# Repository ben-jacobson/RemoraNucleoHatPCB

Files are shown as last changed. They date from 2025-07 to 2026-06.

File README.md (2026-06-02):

# Remora Nucleo-144 Hat PCB.
Work in progress design for a cost-effective, highly customisable LinuxCNC motion control unit.

Form factor is a hat/shield for ST Nucleo-144 evaluation board running [Remora](https://github.com/scottalford75/Remora). Requires a WIZNet TOE for Ethernet control. A link to a specific recommended version of Remora can be found below but other versions should work. This unit is capable of controlling a variety of machine types including CNC milling machines, routers, lathes, laser and plasma cutters. 

Schematics and board layout are editable with Kicad 9. Gerbers and PDF's of the schematics will become available on release. At this stage the design is pre-release with a lot of validation/testing/design work pending. 

## Proposed Features
- **Low cost**: Board can be fabricated via PCBWay, parts can be ordered from Digikey/Mouser/Element14. Digikey part numbers are written into the BOM for easy ordering. My latest build was sponsored by PCBWay but their estimated cost was just under the $100USD mark not including shipping 
- **Approachable**: Goal is to be well documented, providing step by step build guides.
- **Moderate skill requirement**: SMT soldering skills are required but the pad sizes are forgiving enough for hand soldering. Hot air or reflow oven soldering is possible but not required. 

## Current spec
- Nucleo-144 Hat for 6 axis LinuxCNC motion control using custom port of Remora built for STM32. Board may also support GrblHAL but is not yet tested. 
- Up to 6 axes of isolated, step generation. Default max step gen rate in Remora is 40Khz but the driver circuitry has been tested to generate clean step pulses up to 100Khz. Can be used with any 5V single ended or differential stepper driver. Unused axes can be reconfigured as differential digital outputs. 
- IO: 16x digital inputs, 8x NPN digital outputs. Outputs are sink logic/open collector, protected by a fuse and can sink up to 40mA of current. 
- Most outputs can be configured to drive PWM signals, see the readme in the firmware below for available pins and how to configure this.
- IO: 2x analog inputs (non isolated)
- 1x 0-5v / 0-10v DAC for spindle control. Additional spindle control such as direction or indexing can be achieved with IO.
- 24V DC power input for powering the Nucleo which in turn supplies 5V and 3.3V to sections of the board that are isolated. Galvanic isolation between Nucleo and external devices is achieved by supplying your own isolated 24V supply to the separate input. A jumper can be configured on board to powering the board with only one supply, but will break the isolation.  
- Console logging is available via a UART header (TX only, RX is not used by firmware).

## Future Specs
- PSU's seem to be fine handling 18-28V, need to test this before officially marking this as in spec. 
- There is an experimental single ended ABZ Rotary Encoder Input, it was hobbled together from parts already available on the BOM as an experiment. Predictably it does not perform any high speed task, it would probably even struggle with a slowly moved rotary encoder pot. Will eventually replace with a real design. 

## Build guide
This is intended to be a DIY project, not as a complete product.
A link will soon be provided to a place to order on PCBWay, or you can self source the parts using the DigiKey part numbers.
Please see the jumper settings and connecting to USB section as they are contain important information needed to get started.

**Jumper settings:**
Before powering on your Nucleo hat, ensure that the following two jumpers are set: 
JP1: Please remove this jumper entirely
JP3: Place to the far right position, indicating VIN as per the picture in JP3Setting.png

**Connecting to USB:**
Take care when connecting the device to USB. Please make sure that the board is fully powered up before connecting to USB. Failing to do so could result in damage to your computer. This is not an issue with our design, but in the Nucleo itself. For more info see 7.4.2 in the Nucleo 144 datasheet. The device does not need USB to run. USB can be used to flash new firmware or monitor serial output. For serial output, the provided TX pin header is a better choice if you'd like constant serial monitoring during use.

## Todos
- Perform full board testing with a real load and measure current draws, re-design the PSU's for beter efficiency, line/load regulation, ripple rejection, etc. 
- Add PTC resettable fuses to PSU
- Commit release Gerber files to repo and PDF
- Put up some photos of the completed PCB.
- Put up marketplace product on PCBWay
- Research how we might be able to support Servo drives
- Test GRBLHal

## If you'd like to contribute into this project
Reach out - would love some help with any improvement. Would be especially grateful for anyone willing to help with testing, further engineering support, etc.

## Firmware
Firmware can be found in separate repo: https://github.com/ben-jacobson/Remora-STM32F4xx-PIO

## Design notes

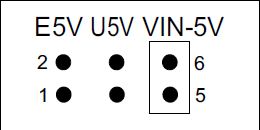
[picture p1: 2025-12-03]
JP3Setting.png

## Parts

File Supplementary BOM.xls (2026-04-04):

Manufacturer | Manufacturer Part Number | Schematic reference | Description | Digikey Part Number | QTY | URL | Per unit cost (AUD at time) | BOM Cost (AUD at time) | Notes | Total Cost (AUD at time) | $42.86
STMicroelectronics | NUCLEO-F446ZE | N/A | STM32F446 Nucleo-144 STM32F4 ARM® Cortex®-M4 MCU 32-Bit Embedded Evaluation Board | 497-16281-ND | 1 | https://www.digikey.com.au/en/products/detail/stmicroelectronics/NUCLEO-F446ZE/5806778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 | $24.56 | $24.56
Wiznet | W5500 Eval Board | N/A | Wiznet Module | N/A | 1 | Ebay/Amazon/AliExpress | - | -
N/A | Nuts and Machine Screws | N/A | Supply own – 5x M2.5 machine screws (3-4mm length). 9x M2.5 Nuts. 2x M3 Nuts | N/A | 1 | N/A | - | -
Würth Elektronik | 971110154 | N/A | 11mm standoff height x M2.5 Standoffs for connecting hat to Nucleo | 732-12923-ND | 4 | https://www.digikey.com.au/en/products/detail/w%C3%BCrth-elektronik/971110154/9488627 | $1.35 | $5.40 | Better value to buy an M2.5 Standoff kit off eBay
Würth Elektronik | 971120154 | N/A | 12mm standoff height x M2.5 Board Standoffs – For mounting Nucleo to DIN Rail mount | 732-12925-ND | 4 | https://www.digikey.com.au/en/products/detail/w%C3%BCrth-elektronik/971120154/9488629 | $1.35 | $5.40
Würth Elektronik | 971200154 | N/A | 20mm Hex Standoff for connecting RPI to hat – M2.5 Brass 0.787" (20.00mm) Silver | 732-12949-ND | 4 | https://www.digikey.com.au/en/products/detail/w%C3%BCrth-elektronik/971200154/9488653 | $1.35 | $5.40
Keystone Electronics | 25503 | N/A | 15mm standoff height x M3 Board Standoffs – 2 for mounting Wiznet Module | 36-25503-ND | 2 | https://www.digikey.com.au/en/products/detail/keystone-electronics/25503/1532182 | $1.05 | $2.10
 | Green = Validated
 | Orange = Altered or yet to be validated
 | Red = Problem, re source

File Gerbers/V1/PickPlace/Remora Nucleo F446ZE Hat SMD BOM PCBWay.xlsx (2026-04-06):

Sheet: Remora Nucleo F446ZE Hat SMD BO
Item # | *Designator | *Qty | Manufacturer | *Mfg Part # | Description / Value | *Package/Footprint | Type | Your Instructions / Notes | US Import Tariff | Note | Part Status | RoHS Status | REACH Status | Moisture Sensitivity Level (MSL) | ECCN | HTSUS | Country of Origin | Environmental Information | Original Part numbers | Unit of Measure | Image | Product Notes
1 | C5,C6 | 2 | Samsung Electro-Mechanics | CL31B105KBHNNNE | CAP CER 1UF 50V X7R 1206 | Capacitor_SMD:C_1206_3216Metric_Pad1.33x1.80mm_HandSolder | SMD | Digikey Part Number: 1276-1068-1-ND |  | - |  | Active | ROHS3 Compliant | REACH Unaffected | 1 (Unlimited) | EAR99 | 8532.24.0020 | Philippines | https://www.samsungsem.com/files/fileDown.do?key=ed1dfdfa-645e-4252-b707-17f9b1502dd1|https://www.samsungsem.com/global/support/certificate/product-stewardship.do | 1276-1068-1-ND | EACH | https://mm.digikey.com/Volume0/opasdata/d220001/medias/images/2537/Ceramic-Capacitor-CL-Series.jpg
2 | C9,C10,C11,C12,C13,C14,C15,C16,C17,C18,C19,C20,C21,C22,C23,C24,C25,C26,C27,C28,C29,C30,C31,C32,C33,C34,C35,C36,C37,C38 | 30 | KEMET | C1206C104K5RACTU | CAP CER 0.1UF 50V X7R 1206 | Capacitor_SMD:C_1206_3216Metric_Pad1.33x1.80mm_HandSolder | SMD | Digikey Part Number: 399-C1206C104K5RACTUCT-ND |  | - |  | Active | ROHS3 Compliant | REACH Unaffected | 1 (Unlimited) | EAR99 | 8532.24.0020 | Mexico |  | 399-C1206C104K5RACTUCT-ND | EACH | https://mm.digikey.com/Volume0/opasdata/d220001/medias/images/721/1206-%283216%29.jpg
3 | D1,D2,D5,D6 | 4 | Harvatek Corporation | B1501USD-20D000313U1930 | 3.2(L) X 1.6(W) X 1.1(H)MM | Diode_SMD:D_1206_3216Metric_Pad1.42x1.75mm_HandSolder | SMD | Digikey Part Number: 3147-B1501USD-20D000313U1930CT-ND |  | - |  | Active | ROHS3 Compliant |  | 2A (4 Weeks) | EAR99 | 8541.41.0000 | Taiwan |  | 3147-B1501USD-20D000313U1930CT-ND | EACH | https://mm.digikey.com/Volume0/opasdata/d220001/derivates/6/003/224/421/MFG_B1501_web%28640x640%29.jpg
4 | D3,D4 | 2 | Diodes Incorporated | B330AF-13 | DIODE SCHOTTKY 30V 3A SMAF | Diode_SMD:D_SMA | SMD | Digikey Part Number: B330AF-13DICT-ND |  | - |  | Active | ROHS3 Compliant | REACH Unaffected | 1 (Unlimited) | EAR99 | 8541.10.0080 | Taiwan | https://mm.digikey.com/Volume0/opasdata/d220001/medias/docus/6731/Diode%20RoHS3%20REACH%20247%20Jan%202025%20Statement.pdf | B330AF-13DICT-ND | EACH | https://mm.digikey.com/Volume0/opasdata/d220001/medias/images/6210/31%7ESMAFLAT%7E%7E2.jpg
5 | D7,D8 | 2 | onsemi | SZMMBZ5232BLT1G | DIODE ZENER 5.6V 225MW SOT23-3 | Package_TO_SOT_SMD:SOT-23 | SMD | Digikey Part Number: SZMMBZ5232BLT1GOSCT-ND |  | - |  | Active | ROHS3 Compliant | REACH Unaffected | 1 (Unlimited) | EAR99 | 8541.10.0050 | China | https://www.onsemi.com/site/pdf/RoHS-statement.pdf|https://www.onsemi.com/site/pdf/REACH-compliance-statement.pdf|https://www.onsemi.com/PowerSolutions/MaterialComposition.do?export=pdf&opnId=SZMMBZ5232BLT1G | SZMMBZ5232BLT1GOSCT-ND | EACH | https://mm.digikey.com/Volume0/opasdata/d220001/medias/images/5883/488%7E318-08%7EET%2CL%2CLT%2CSF%2CSN%7E3.jpg
6 | F1,F2,F3,F4,F5,F6,F7,F8,F9,F10,F11 | 11 | Murata Electronics | PRG18BB330MB1RB | PTC RESET FUSE 24V 36MA 0603 | Fuse:Fuse_0603_1608Metric_Pad1.05x0.95mm_HandSolder | SMD | Digikey Part Number: 490-2471-1-ND |  | - |  | Active | ROHS3 Compliant | REACH Unaffected | 1 (Unlimited) | EAR99 | 8533.40.8070 | China |  | 490-2471-1-ND | EACH | https://mm.digikey.com/Volume0/opasdata/d220001/medias/images/2439/490-PTC%20RESET%200603%20SERIES.jpg
7 | L1,L2 | 2 | Bourns Inc. | SDE0805A-680K | FIXED IND 68UH 1.45A 280 MOHM | Inductor_SMD:L_APV_ANR8040 | SMD | Digikey Part Number: SDE0805A-680KCT-ND |  | - |  | Active | ROHS3 Compliant | REACH Unaffected | 1 (Unlimited) | EAR99 | 8504.50.4000 | China | https://mm.digikey.com/Volume0/opasdata/d220001/medias/docus/6657/Bourns%20REACH%20247%20Jan%202025%20Statement.pdf|https://www.bourns.com/docs/rohs-cofc/cofc_sde.pdf?sfvrsn=510e6dd9_2 | SDE0805A-680KCT-ND | EACH | https://mm.digikey.com/Volume0/opasdata/d220001/medias/images/2605/MFG_SDE0805A%20Series.jpg
8 | Q1 | 1 | onsemi | BC847CLT1G | TRANS NPN 45V 0.1A SOT23-3 | Package_TO_SOT_SMD:SOT-23 | SMD | Digikey Part Number: BC847CLT1GOSCT-ND |  | - |  | Active | ROHS3 Compliant | REACH Unaffected | 1 (Unlimited) | EAR99 | 8541.21.0075 | China | https://www.onsemi.com/site/pdf/RoHS-statement.pdf|https://www.onsemi.com/PowerSolutions/MaterialComposition.do?export=pdf&opnId=BC847CLT1G | BC847CLT1GOSCT-ND | EACH | https://mm.digikey.com/Volume0/opasdata/d220001/medias/images/5883/488%7E318-08%7EET%2CL%2CLT%2CSF%2CSN%7E3.jpg
9 | R1,R21,R22,R23,R24,R25,R26,R27,R28,R61,R62,R63,R64,R65,R66,R67,R68,R77,R78,R79,R80,R81,R82,R83,R84,R89,R90,R95,R96,R97,R100 | 31 | YAGEO | RC1206FR-074K7L | RES 4.7K OHM 1% 1/4W 1206 | Resistor_SMD:R_1206_3216Metric_Pad1.30x1.75mm_HandSolder | SMD | Digikey Part Number: 311-4.70KFRCT-ND |  | - |  | Active | ROHS3 Compliant | REACH Unaffected | 1 (Unlimited) | EAR99 | 8533.21.0030 | Taiwan | https://www.yageogroup.com/content/Resource%20Library/Product%20Environmental%20Compliance/RoHS_Compliance_YAGEO.pdf | 311-4.70KFRCT-ND | EACH | https://mm.digikey.com/Volume0/opasdata/d220001/medias/images/4322/cut-tape-render.jpg
10 | R2,R3,R10,R11,R12,R13,R14,R15,R16,R17,R18,R19,R20,R29,R30,R31,R32,R33,R34,R35,R36,R37,R38,R39,R40,R41,R42,R43,R44,R45,R46,R47,R48,R49,R50,R51,R52,R53,R54,R55,R56,R57,R58,R59,R60,R69,R70,R71,R72,R73,R74,R75,R76,R94 | 54 | YAGEO | RC1206FR-07180RL | RES 180 OHM 1% 1/4W 1206 | Resistor_SMD:R_1206_3216Metric_Pad1.30x1.75mm_HandSolder | SMD | Digikey Part Number: 311-180FRCT-ND |  | - |  | Active | ROHS3 Compliant | REACH Unaffected | 1 (Unlimited) | EAR99 | 8533.21.0030 | Taiwan | https://www.yageogroup.com/content/Resource%20Library/Product%20Environmental%20Compliance/RoHS_Compliance_YAGEO.pdf | 311-180FRCT-ND | EACH | https://mm.digikey.com/Volume0/opasdata/d220001/medias/images/4842/Yageo-0603.jpg
11 | R85,R86,R87,R88,R91,R92,R93,R99,R101 | 9 | Stackpole Electronics Inc | RMCF1206JT1K20 | RES 1.2K OHM 5% 1/4W 1206 | Resistor_SMD:R_1206_3216Metric_Pad1.30x1.75mm_HandSolder | SMD | Digikey Part Number: RMCF1206JT1K20CT-ND |  | - |  | Active | ROHS3 Compliant | REACH Unaffected | 1 (Unlimited) | EAR99 | 8533.21.0030 | China | https://www.seielect.com/catalog/SEI-RoHS_Compliance_Status.pdf|https://www.seielect.com/catalog/reach.pdf|https://www.seielect.com/catalog/sei-coc%20prop%2065.pdf | RMCF1206JT1K20CT-ND | EACH | https://mm.digikey.com/Volume0/opasdata/d220001/medias/images/4849/738_1206.jpg
12 | R98 | 1 | YAGEO | RC1206FR-0710KL | RES 10K OHM 1% 1/4W 1206 | Resistor_SMD:R_1206_3216Metric_Pad1.30x1.75mm_HandSolder | SMD | Digikey Part Number: 311-10.0KFRCT-ND |  | - |  | Active | ROHS3 Compliant | REACH Unaffected | 1 (Unlimited) | EAR99 | 8533.21.0030 | Taiwan | https://www.yageogroup.com/content/Resource%20Library/Product%20Environmental%20Compliance/RoHS_Compliance_YAGEO.pdf | 311-10.0KFRCT-ND | EACH | https://mm.digikey.com/Volume0/opasdata/d220001/medias/images/4322/cut-tape-render.jpg
13 | SW1 | 1 | Omron Electronics Inc-EMC Div | B3FS-1002P | SWITCH TACTILE SPST-NO 0.05A 24V | Button_Switch_SMD:SW_SPST_Omron_B3FS-100xP | SMD | Digikey Part Number: SW424CT-ND |  | - |  | Active | ROHS3 Compliant | REACH Unaffected | 1 (Unlimited) | EAR99 | 8536.50.9031 | China |  | SW424CT-ND | EACH | https://mm.digikey.com/Volume0/opasdata/d220001/medias/images/999/B3FS-1002PCHN.jpg
14 | U2 | 1 | UMW | XL1509-12 | IC REG BUCK 5.0V 2A 8SOIC | Package_SO:SOIC-8_3.9x4.9mm_P1.27mm | SMD | Digikey Part Number: 4518-XL1509-12CT-ND |  | - |  | Active | ROHS3 Compliant | REACH Unaffected | 1 (Unlimited) | EAR99 | 8542.39.0060 | China |  | 4518-XL1509-12CT-ND | EACH | https://mm.digikey.com/Volume0/opasdata/d220001/derivates/6/003/215/772/MFG_4518_SOP-8_web%28640x640%29.jpg
15 | U3 | 1 | UMW | XL1509-5.0 | IC REG BUCK 5.0V 2A 8SOIC | Package_SO:SOIC-8_3.9x4.9mm_P1.27mm | SMD | Digikey Part Number: 4518-XL1509-5.0CT-ND |  | - |  | Active | ROHS3 Compliant | REACH Unaffected | 1 (Unlimited) | EAR99 | 8542.39.0060 | China |  | 4518-XL1509-5.0CT-ND | EACH | https://mm.digikey.com/Volume0/opasdata/d220001/derivates/6/003/215/772/MFG_4518_SOP-8_web%28640x640%29.jpg
16 | U4,U6,U7,U8,U9,U10,U11,U12,U14,U17 | 10 | Lite-On Inc. | LTV-247 | OPTOISO 3.75KV 4CH TRANS 16-SO | Package_SO:SOP-16_4.4x10.4mm_P1.27mm | SMD | Digikey Part Number: 160-2255-1-ND |  | - |  | Active | ROHS3 Compliant | REACH Unaffected | 1 (Unlimited) | EAR99 | 8541.49.8000 | China |  | 160-2255-1-ND | EACH | https://mm.digikey.com/Volume0/opasdata/d220001/medias/images/2476/16%20SOIC.jpg
17 | U5,U13,U15 | 3 | Texas Instruments | AM26LS31CDR | IC TRANSCEIVER 4/0 16SOIC | Package_SO:SOIC-16_3.9x9.9mm_P1.27mm | SMD | Digikey Part Number: 296-1010-1-ND |  | - |  | Active | ROHS3 Compliant | REACH Unaffected | 1 (Unlimited) | EAR99 | 8542.39.0070 | Mexico |  | 296-1010-1-ND | EACH | https://mm.digikey.com/Volume0/opasdata/d220001/medias/images/3982/296%7E4040047-6%7ED%7E16.JPG
18 | U16 | 1 | Microchip Technology | MCP6042T-E/MSVAO | IC OPAMP GP 2 CIRCUIT 8SOIC | Package_SO:SOIC-8_3.9x4.9mm_P1.27mm | SMD | Digikey Part Number: 150-MCP6042T-E/MSVAOCT-ND |  | - |  | Active | ROHS3 Compliant | REACH Unaffected | 2 (1 Year) | EAR99 | 8542.33.0001 | Thailand | https://ww1.microchip.com/downloads/aemDocuments/documents/corporate-responsibilty/environmental/product-regulatory-information/Semiconductor_EnvCoC.pdf|https://ww1.microchip.com/downloads/aemDocuments/documents/corporate-responsibilty/environmental/product-regulatory-information/Microchip_REACH_Statement.pdf | 150-MCP6042T-E/MSVAOCT-ND | EACH | https://mm.digikey.com/Volume0/opasdata/d220001/derivates/6/003/245/611/MFG_150%7EC04-057%7ESN%2COA%7E8_web%28640x640%29.jpg
19 | U18 | 1 | Diotec Semiconductor | MMTL431A | IC VREF SHUNT ADJ 0.5% SOT23-3 | Package_TO_SOT_SMD:SOT-23 | SMD | Digikey Part Number: 4878-MMTL431ACT-ND |  | - |  | Active | ROHS3 Compliant | REACH Unaffected | Not Applicable | EAR99 | 8542.39.0070 | China | https://diotec.com/request/imds/p200_e.pdf | 4878-MMTL431ACT-ND | EACH | https://mm.digikey.com/Volume0/opasdata/d220001/derivates/6/003/243/004/MFG_4878%7ESOT23-3%7E%7E3_web%28640x640%29.jpg

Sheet: Sheet2
 |  |  | Remora Nucleo F446ZE Hat BOM
Item # | *Designator | *Qty | Manufacturer | *Mfg Part # | Description / Value | *Package/Footprint | Type | Your Instructions / Notes
1 | C5,C6 | 2 | Samsung Electro-Mechanics | CL31B105KBHNNNE | CAP CER 1UF 50V X7R 1206 | Capacitor_SMD:C_1206_3216Metric_Pad1.33x1.80mm_HandSolder | SMD | Digikey Part Number: 1276-1068-1-ND
2 | C9,C10,C11,C12,C13,C14,C15,C16,C17,C18,C19,C20,C21,C22,C23,C24,C25,C26,C27,C28,C29,C30,C31,C32,C33,C34,C35,C36,C37,C38 | 30 | KEMET | C1206C104K5RACTU | CAP CER 0.1UF 50V X7R 1206 | Capacitor_SMD:C_1206_3216Metric_Pad1.33x1.80mm_HandSolder | SMD | Digikey Part Number: 399-C1206C104K5RACTUCT-ND
3 | D1,D2,D5,D6 | 4 | Harvatek Corporation | B1501USD-20D000313U1930 | 3.2(L) X 1.6(W) X 1.1(H)MM | Diode_SMD:D_1206_3216Metric_Pad1.42x1.75mm_HandSolder | SMD | Digikey Part Number: 3147-B1501USD-20D000313U1930CT-ND
4 | D3,D4 | 2 | Diodes Incorporated | B330AF-13 | DIODE SCHOTTKY 30V 3A SMAF | Diode_SMD:D_SMA | SMD | Digikey Part Number: B330AF-13DICT-ND
5 | D7,D8 | 2 | onsemi | SZMMBZ5232BLT1G | DIODE ZENER 5.6V 225MW SOT23-3 | Package_TO_SOT_SMD:SOT-23 | SMD | Digikey Part Number: SZMMBZ5232BLT1GOSCT-ND
6 | F1,F2,F3,F4,F5,F6,F7,F8,F9,F10,F11 | 11 | Murata Electronics | PRG18BB330MB1RB | PTC RESET FUSE 24V 36MA 0603 | Fuse:Fuse_0603_1608Metric_Pad1.05x0.95mm_HandSolder | SMD | Digikey Part Number: 490-2471-1-ND
7 | L1,L2 | 2 | Bourns Inc. | SDE0805A-680K | FIXED IND 68UH 1.45A 280 MOHM | Inductor_SMD:L_APV_ANR8040 | SMD | Digikey Part Number: SDE0805A-680KCT-ND
8 | Q1 | 1 | onsemi | BC847CLT1G | TRANS NPN 45V 0.1A SOT23-3 | Package_TO_SOT_SMD:SOT-23 | SMD | Digikey Part Number: BC847CLT1GOSCT-ND
9 | R1,R21,R22,R23,R24,R25,R26,R27,R28,R61,R62,R63,R64,R65,R66,R67,R68,R77,R78,R79,R80,R81,R82,R83,R84,R89,R90,R95,R96,R97,R100 | 31 | YAGEO | RC1206FR-074K7L | RES 4.7K OHM 1% 1/4W 1206 | Resistor_SMD:R_1206_3216Metric_Pad1.30x1.75mm_HandSolder | SMD | Digikey Part Number: 311-4.70KFRCT-ND
10 | R2,R3,R10,R11,R12,R13,R14,R15,R16,R17,R18,R19,R20,R29,R30,R31,R32,R33,R34,R35,R36,R37,R38,R39,R40,R41,R42,R43,R44,R45,R46,R47,R48,R49,R50,R51,R52,R53,R54,R55,R56,R57,R58,R59,R60,R69,R70,R71,R72,R73,R74,R75,R76,R94 | 54 | YAGEO | RC1206FR-07180RL | RES 180 OHM 1% 1/4W 1206 | Resistor_SMD:R_1206_3216Metric_Pad1.30x1.75mm_HandSolder | SMD | Digikey Part Number: 311-180FRCT-ND
11 | R85,R86,R87,R88,R91,R92,R93,R99,R101 | 9 | Stackpole Electronics Inc | RMCF1206JT1K20 | RES 1.2K OHM 5% 1/4W 1206 | Resistor_SMD:R_1206_3216Metric_Pad1.30x1.75mm_HandSolder | SMD | Digikey Part Number: RMCF1206JT1K20CT-ND
12 | R98 | 1 | YAGEO | RC1206FR-0710KL | RES 10K OHM 1% 1/4W 1206 | Resistor_SMD:R_1206_3216Metric_Pad1.30x1.75mm_HandSolder | SMD | Digikey Part Number: 311-10.0KFRCT-ND
13 | SW1 | 1 | Omron Electronics Inc-EMC Div | B3FS-1002P | SWITCH TACTILE SPST-NO 0.05A 24V | Button_Switch_SMD:SW_SPST_Omron_B3FS-100xP | SMD | Digikey Part Number: SW424CT-ND
14 | U2 | 1 | UMW | XL1509-12 | IC REG BUCK 5.0V 2A 8SOIC | Package_SO:SOIC-8_3.9x4.9mm_P1.27mm | SMD | Digikey Part Number: 4518-XL1509-12CT-ND
15 | U3 | 1 | UMW | XL1509-5.0 | IC REG BUCK 5.0V 2A 8SOIC | Package_SO:SOIC-8_3.9x4.9mm_P1.27mm | SMD | Digikey Part Number: 4518-XL1509-5.0CT-ND
16 | U4,U6,U7,U8,U9,U10,U11,U12,U14,U17 | 10 | Lite-On Inc. | LTV-247 | OPTOISO 3.75KV 4CH TRANS 16-SO | Package_SO:SOP-16_4.4x10.4mm_P1.27mm | SMD | Digikey Part Number: 160-2255-1-ND
17 | U5,U13,U15 | 3 | Texas Instruments | AM26LS31CDR | IC TRANSCEIVER 4/0 16SOIC | Package_SO:SOIC-16_3.9x9.9mm_P1.27mm | SMD | Digikey Part Number: 296-1010-1-ND
18 | U16 | 1 | Microchip Technology | MCP6042T-E/MSVAO | IC OPAMP GP 2 CIRCUIT 8SOIC | Package_SO:SOIC-8_3.9x4.9mm_P1.27mm | SMD | Digikey Part Number: 150-MCP6042T-E/MSVAOCT-ND
19 | U18 | 1 | Diotec Semiconductor | MMTL431A | IC VREF SHUNT ADJ 0.5% SOT23-3 | Package_TO_SOT_SMD:SOT-23 | SMD | Digikey Part Number: 4878-MMTL431ACT-ND
Need a quick and accurante quote? Need an efficient production? Please read SMT Ordering Necessary Files & Info in 1 minute. Thank you very much! (https://www.pcbway.com/smt_ordering_guide.html)
Click for Instructions on How to Create a BOM (https://www.pcbway.com/blog/PCB_Assembly/How_to_Build_a_BOM__Bill_Of_Materials_.html)

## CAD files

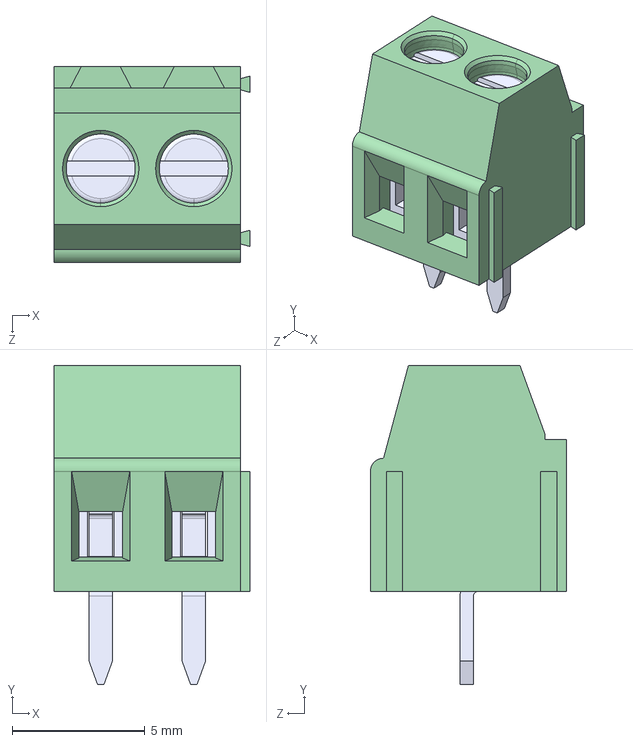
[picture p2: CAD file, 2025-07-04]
Adam Tech Footprints/EBWA_02_A/EBWA-02-A.step
7.37 x 12.0 x 7.39 mm

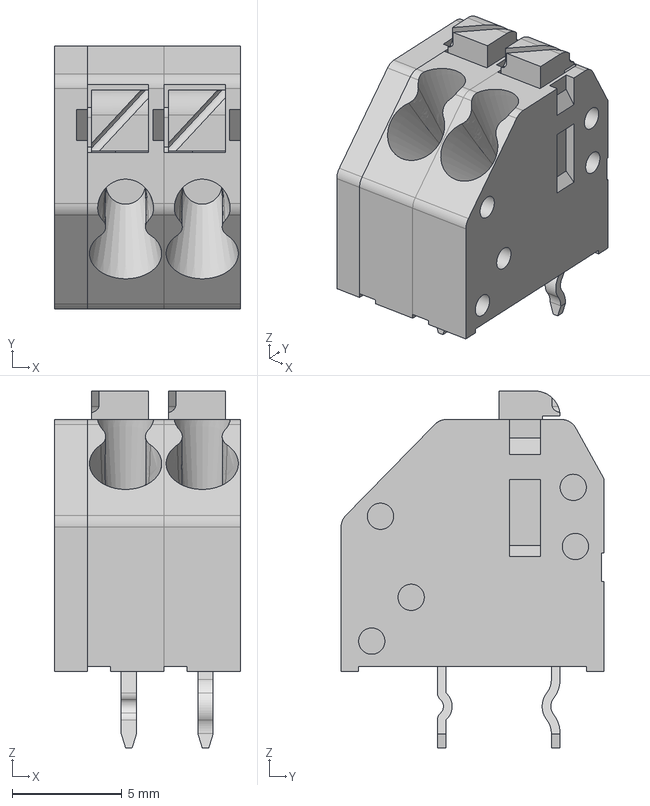
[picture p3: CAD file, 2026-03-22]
TerminalConnectors/691412120002B/Download_STP_691412120002B+(rev1).stp
8.50 x 12.0 x 16.3 mm
6914121200xxB_CAPOT
6914121200xx
6914121200xx_levier x 2
6914121200xxB x 2
6914121200xx_LONG

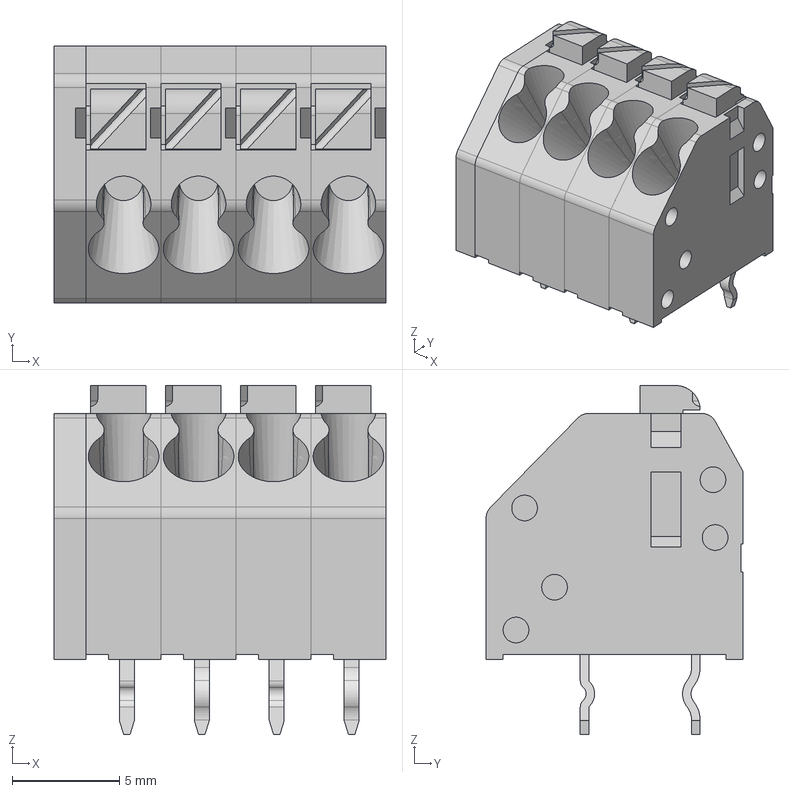
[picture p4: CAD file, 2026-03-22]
TerminalConnectors/691412120004B/691412120004B+(rev1).stp
15.5 x 12.0 x 16.3 mm
6914121200xxB_CAPOT
6914121200xx x 2
6914121200xx_levier x 4
6914121200xxB x 4
6914121200xx_LONG x 2

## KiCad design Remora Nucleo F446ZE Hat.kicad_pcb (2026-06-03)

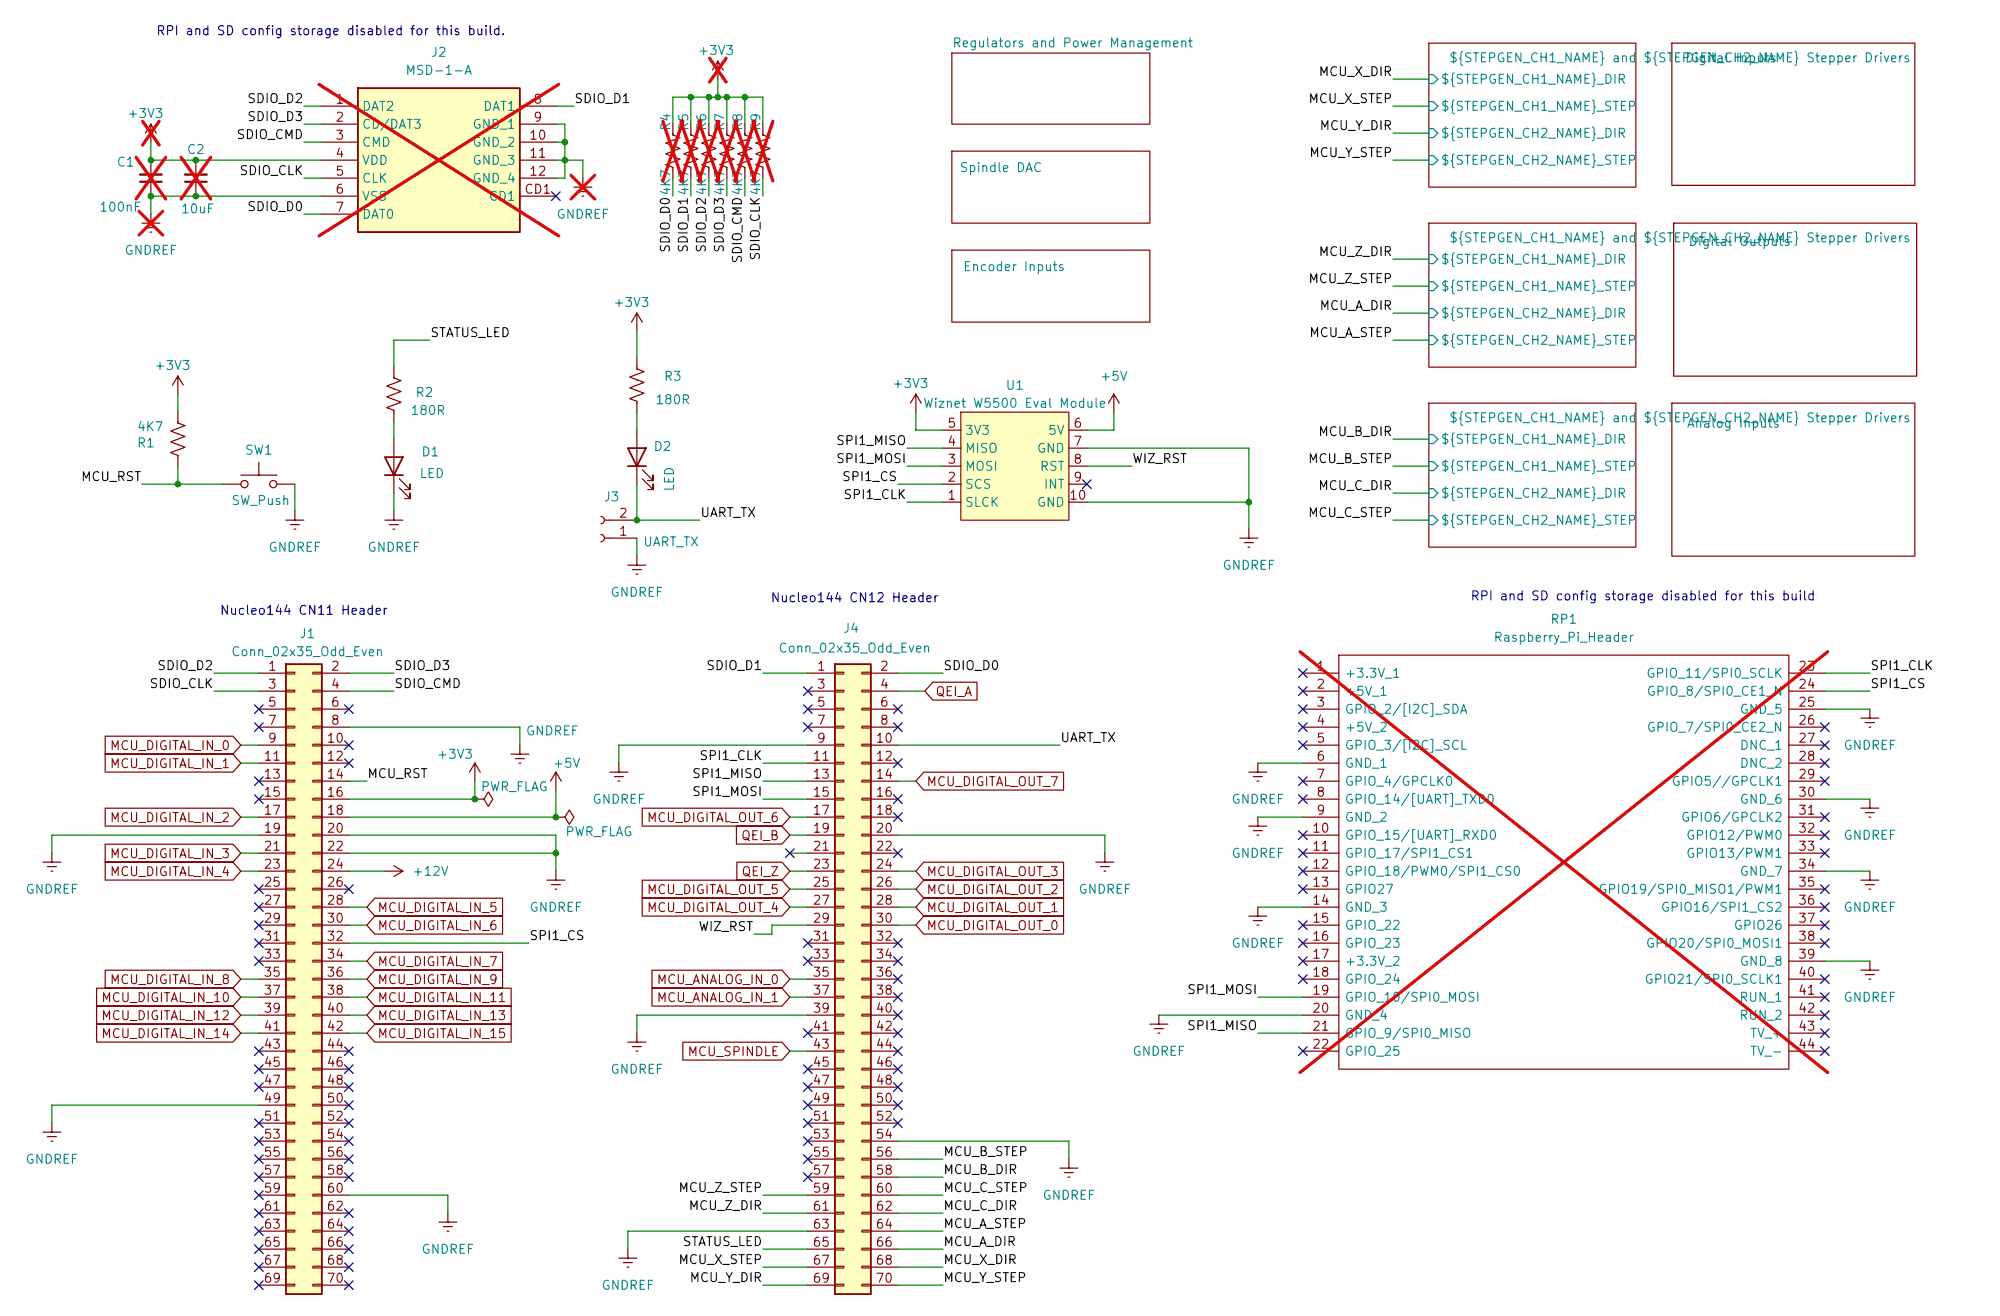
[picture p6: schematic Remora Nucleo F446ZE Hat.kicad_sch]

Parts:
C1: 100nF; C_1206_3216Metric_Pad1.33x1.80mm_HandSolder; Digikey Part Number 399-C1206C104K5RACTUCT-ND; not fitted
C2: 10uF; C_1206_3216Metric_Pad1.33x1.80mm_HandSolder; Digikey Part Number 1276-1804-1-ND; not fitted
D1, D2: LED; D_1206_3216Metric_Pad1.42x1.75mm_HandSolder; Digikey Part Number 3147-B1501USD-20D000313U1930CT-ND
J1, J4: Conn_02x35_Odd_Even; PinHeader_2x35_P2.54mm_Vertical; Digikey Part Number SSW-135-03-T-D-ND
J2: MSD-1-A; MSD1A; Manufacturer_Part_Number MSD-1-A; Mouser Part Number 179-MSD-1-A; not fitted
J3: UART_TX; PinHeader_1x02_P2.54mm_Vertical; Digikey Part Number PH1-02-UA
R1: 4K7; R_1206_3216Metric_Pad1.30x1.75mm_HandSolder; Digikey Part Number 311-4.70KFRCT-ND
R2, R3: 180R; R_1206_3216Metric_Pad1.30x1.75mm_HandSolder; Digikey Part Number 311-180FRCT-ND
R4, R5, R6, R7, R8, R9: 4K7; R_1206_3216Metric_Pad1.30x1.75mm_HandSolder; Digikey Part Number 311-4.70KFRCT-ND; not fitted
RP1: Raspberry_Pi_Header; raspberrypi_2_3; Manufacturer_Part_Number Raspberry Pi 2 or 3; Digikey Part Number SAM1204-20-ND; not fitted
SW1: SW_Push; SW_SPST_Omron_B3FS-100xP; Digikey Part Number SW424CT-ND
U1: Wiznet W5500 Eval Module; W5500EvalModule; Digikey Part Number SAM12520-ND

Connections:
+3V3: C1.2, C2.2, J1.16, J2.4 (VDD), R1.1, R3.1, R4.1, R5.1, R6.1, R7.1, R8.1, R9.1, U1.5 (3V3); also elsewhere on the board
+5V: J1.18, U1.6 (5V)
+12V: J1.24; also elsewhere on the board
/MCU_A_DIR: J4.66; also elsewhere on the board
/MCU_A_STEP: J4.64; also elsewhere on the board
/MCU_B_DIR: J4.58; also elsewhere on the board
/MCU_B_STEP: J4.56; also elsewhere on the board
/MCU_C_DIR: J4.62; also elsewhere on the board
/MCU_C_STEP: J4.60; also elsewhere on the board
/MCU_RST: J1.14, R1.2, SW1.1
/MCU_X_DIR: J4.68; also elsewhere on the board
/MCU_X_STEP: J4.67; also elsewhere on the board
/MCU_Y_DIR: J4.69; also elsewhere on the board
/MCU_Y_STEP: J4.70; also elsewhere on the board
/MCU_Z_DIR: J4.61; also elsewhere on the board
/MCU_Z_STEP: J4.59; also elsewhere on the board
/SDIO_CLK: J1.3, J2.5 (CLK), R9.2
/SDIO_CMD: J1.4, J2.3 (CMD), R8.2
/SDIO_D0: J2.7 (DAT0), J4.2, R4.2
/SDIO_D1: J2.8 (DAT1), J4.1, R5.2
/SDIO_D2: J1.1, J2.1 (DAT2), R6.2
/SDIO_D3: J1.2, J2.2 (CD/DAT3), R7.2
/SPI1_CLK: J4.11, RP1.23 (GPIO_11/SPI0_SCLK), U1.1 (SLCK)
/SPI1_CS: J1.32, RP1.24 (GPIO_8/SPI0_CE1_N), U1.2 (SCS)
/SPI1_MISO: J4.13, RP1.21 (GPIO_9/SPI0_MISO), U1.4 (MISO)
/SPI1_MOSI: J4.15, RP1.19 (GPIO_10/SPI0_MOSI), U1.3 (MOSI)
/STATUS_LED: J4.65, R2.1
/UART_TX: D2.1 (K), J3.2, J4.10
/WIZ_RST: J4.29, U1.8 (RST)
GNDREF: C1.1, C2.1, D1.1 (K), J1.8, J1.19, J1.20, J1.22, J1.49, J1.60, J2.6 (VSS), J2.9 (GND_1), J2.10 (GND_2), J2.11 (GND_3), J2.12 (GND_4), J3.1, J4.9, J4.20, J4.39, J4.54, J4.63, RP1.6 (GND_1), RP1.9 (GND_2), RP1.14 (GND_3), RP1.20 (GND_4), RP1.25 (GND_5), RP1.30 (GND_6), RP1.34 (GND_7), RP1.39 (GND_8), SW1.2, U1.7 (GND), U1.10 (GND); also elsewhere on the board
MCU_ANALOG_IN_0: J4.35; also elsewhere on the board
MCU_ANALOG_IN_1: J4.37; also elsewhere on the board
MCU_DIGITAL_IN_0: J1.9; also elsewhere on the board
MCU_DIGITAL_IN_1: J1.11; also elsewhere on the board
MCU_DIGITAL_IN_2: J1.17; also elsewhere on the board
MCU_DIGITAL_IN_3: J1.21; also elsewhere on the board
MCU_DIGITAL_IN_4: J1.23; also elsewhere on the board
MCU_DIGITAL_IN_5: J1.28; also elsewhere on the board
MCU_DIGITAL_IN_6: J1.30; also elsewhere on the board
MCU_DIGITAL_IN_7: J1.34; also elsewhere on the board
MCU_DIGITAL_IN_8: J1.35; also elsewhere on the board
MCU_DIGITAL_IN_9: J1.36; also elsewhere on the board
MCU_DIGITAL_IN_10: J1.37; also elsewhere on the board
MCU_DIGITAL_IN_11: J1.38; also elsewhere on the board
MCU_DIGITAL_IN_12: J1.39; also elsewhere on the board
MCU_DIGITAL_IN_13: J1.40; also elsewhere on the board
MCU_DIGITAL_IN_14: J1.41; also elsewhere on the board
MCU_DIGITAL_IN_15: J1.42; also elsewhere on the board
MCU_DIGITAL_OUT_0: J4.30; also elsewhere on the board
MCU_DIGITAL_OUT_1: J4.28; also elsewhere on the board
MCU_DIGITAL_OUT_2: J4.26; also elsewhere on the board
MCU_DIGITAL_OUT_3: J4.24; also elsewhere on the board
MCU_DIGITAL_OUT_4: J4.27; also elsewhere on the board
MCU_DIGITAL_OUT_5: J4.25; also elsewhere on the board
MCU_DIGITAL_OUT_6: J4.17; also elsewhere on the board
MCU_DIGITAL_OUT_7: J4.14; also elsewhere on the board
MCU_SPINDLE: J4.43; also elsewhere on the board
unnamed: D1.2 (A), R2.2
unnamed: D2.2 (A), R3.2
QEI_A: J4.4; also elsewhere on the board
QEI_B: J4.19; also elsewhere on the board
QEI_Z: J4.23; also elsewhere on the board

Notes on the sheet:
RPI and SD config storage disabled for this build.
RPI and SD config storage disabled for this build
Nucleo144 CN12 Header
Nucleo144 CN11 Header

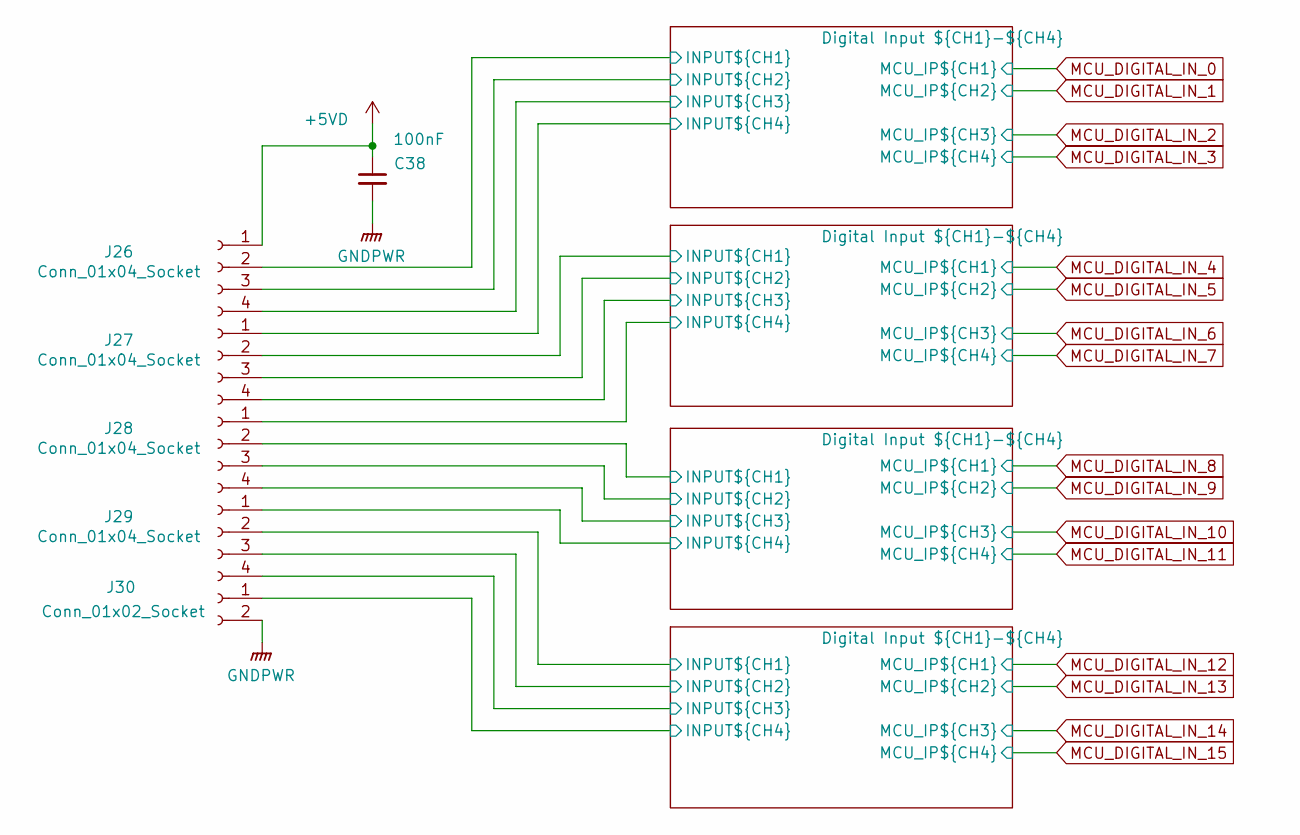
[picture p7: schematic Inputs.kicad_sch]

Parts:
C38: 100nF; C_1206_3216Metric_Pad1.33x1.80mm_HandSolder; Digikey Part Number 399-C1206C104K5RACTUCT-ND
J26, J27, J28, J29: Conn_01x04_Socket; 691412120004B; Digikey Part Number 732-691412120004B-ND
J30: Conn_01x02_Socket; 691412120002B; Digikey Part Number 732-691412120002B-ND

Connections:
+5VD: C38.1, J26.1; also elsewhere on the board
/Digital Inputs/Digital Input 0-3/INPUT0: J26.2; also elsewhere on the board
/Digital Inputs/Digital Input 0-3/INPUT1: J26.3; also elsewhere on the board
/Digital Inputs/Digital Input 0-3/INPUT2: J26.4; also elsewhere on the board
/Digital Inputs/Digital Input 0-3/INPUT3: J27.1; also elsewhere on the board
/Digital Inputs/Digital Input 4-7/INPUT4: J27.2; also elsewhere on the board
/Digital Inputs/Digital Input 4-7/INPUT5: J27.3; also elsewhere on the board
/Digital Inputs/Digital Input 4-7/INPUT6: J27.4; also elsewhere on the board
/Digital Inputs/Digital Input 4-7/INPUT7: J28.1; also elsewhere on the board
/Digital Inputs/Digital Input 8-11/INPUT8: J28.2; also elsewhere on the board
/Digital Inputs/Digital Input 8-11/INPUT9: J28.3; also elsewhere on the board
/Digital Inputs/Digital Input 8-11/INPUT10: J28.4; also elsewhere on the board
/Digital Inputs/Digital Input 8-11/INPUT11: J29.1; also elsewhere on the board
/Digital Inputs/Digital Input 12-15/INPUT12: J29.2; also elsewhere on the board
/Digital Inputs/Digital Input 12-15/INPUT13: J29.3; also elsewhere on the board
/Digital Inputs/Digital Input 12-15/INPUT14: J29.4; also elsewhere on the board
/Digital Inputs/Digital Input 12-15/INPUT15: J30.1; also elsewhere on the board
GNDPWR: C38.2, J30.2; also elsewhere on the board

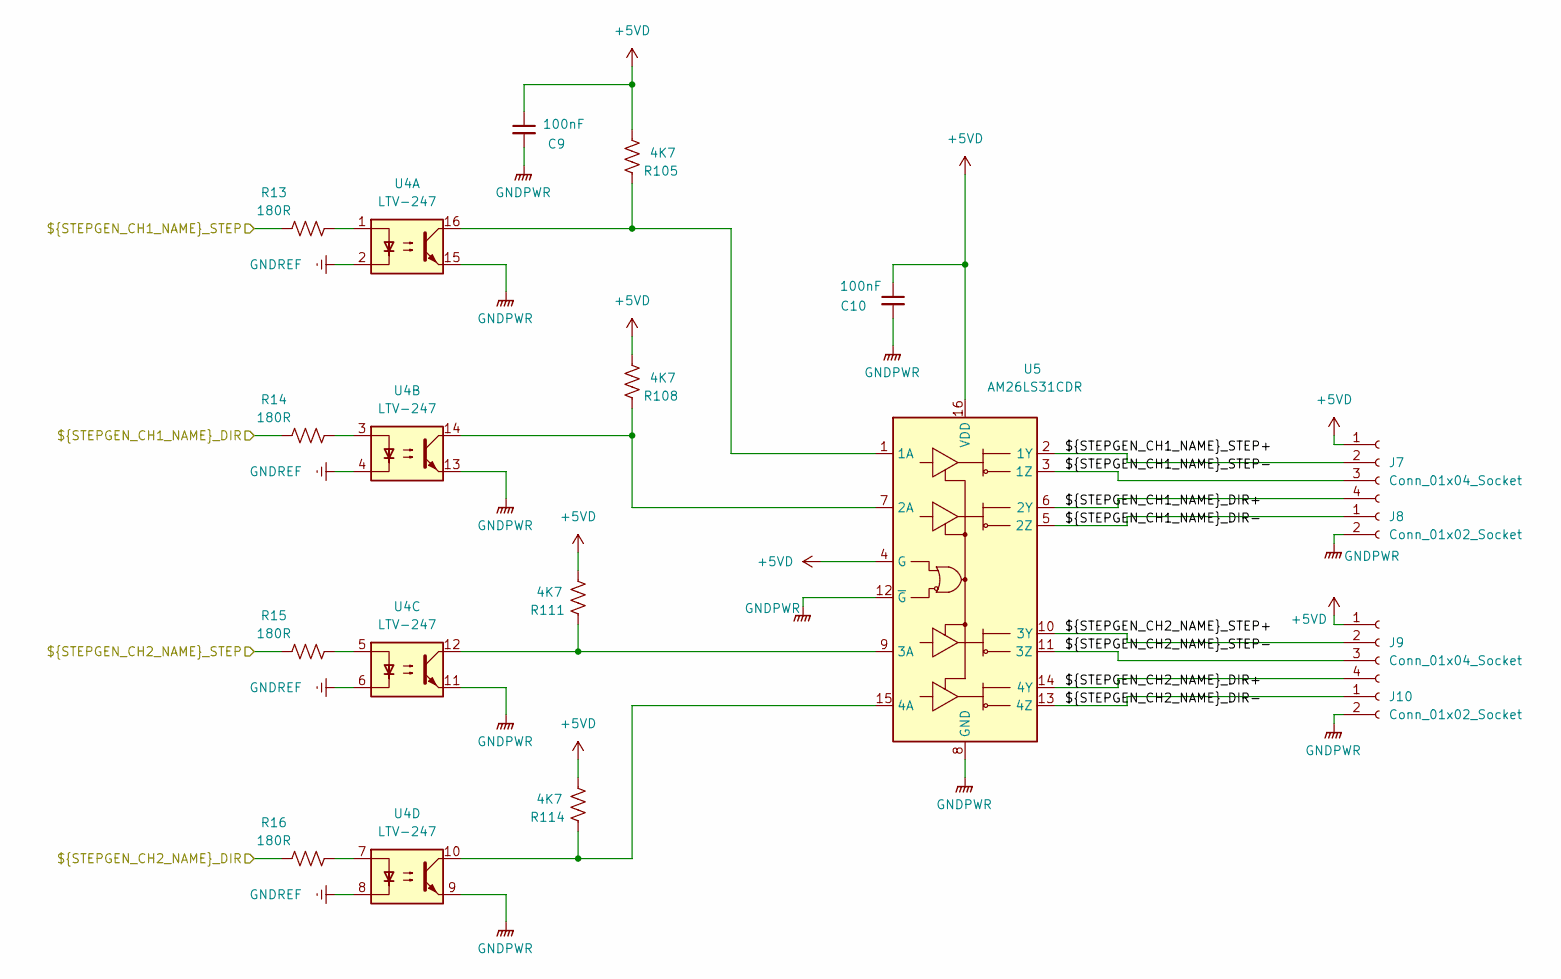
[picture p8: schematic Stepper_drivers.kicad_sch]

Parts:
C9, C10: 100nF; C_1206_3216Metric_Pad1.33x1.80mm_HandSolder; Digikey Part Number 399-C1206C104K5RACTUCT-ND
J7, J9: Conn_01x04_Socket; 691412120004B; Digikey Part Number 732-691412120004B-ND
J8, J10: Conn_01x02_Socket; 691412120002B; Digikey Part Number 732-691412120002B-ND
R13, R14, R15, R16: 180R; R_1206_3216Metric_Pad1.30x1.75mm_HandSolder; Digikey Part Number 311-180FRCT-ND
R105, R108, R111, R114: 4K7; R_1206_3216Metric_Pad1.30x1.75mm_HandSolder; Digikey Part Number 311-4.70KFRCT-ND
U4: LTV-247; SOP-16_4.4x10.4mm_P1.27mm; Digikey Part Number 160-2255-1-ND
U5: AM26LS31CDR; SOIC-16_3.9x9.9mm_P1.27mm; JLCPCB Part #（optional） C3019542

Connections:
+5VD: C9.1, C10.1, J7.1, J9.1, R105.2, R108.2, R111.2, R114.2, U5.4 (G), U5.16 (VDD); also elsewhere on the board
/MCU_X_DIR: R14.1; also elsewhere on the board
/MCU_X_STEP: R13.1; also elsewhere on the board
/MCU_Y_DIR: R16.1; also elsewhere on the board
/MCU_Y_STEP: R15.1; also elsewhere on the board
/X and Y Stepper Drivers/X_DIR+: J7.4, U5.6 (2Y)
/X and Y Stepper Drivers/X_DIR-: J8.1, U5.5 (2Z)
/X and Y Stepper Drivers/X_STEP+: J7.2, U5.2 (1Y)
/X and Y Stepper Drivers/X_STEP-: J7.3, U5.3 (1Z)
/X and Y Stepper Drivers/Y_DIR+: J9.4, U5.14 (4Y)
/X and Y Stepper Drivers/Y_DIR-: J10.1, U5.13 (4Z)
/X and Y Stepper Drivers/Y_STEP+: J9.2, U5.10 (3Y)
/X and Y Stepper Drivers/Y_STEP-: J9.3, U5.11 (3Z)
GNDPWR: C9.2, C10.2, J8.2, J10.2, U4.9, U4.11, U4.13, U4.15, U5.8 (GND), U5.12 (~G); also elsewhere on the board
GNDREF: U4.2, U4.4, U4.6, U4.8; also elsewhere on the board
unnamed: R13.2, U4.1
unnamed: R14.2, U4.3
unnamed: R15.2, U4.5
unnamed: R16.2, U4.7
unnamed: R105.1, U4.16, U5.1 (1A)
unnamed: R108.1, U4.14, U5.7 (2A)
unnamed: R111.1, U4.12, U5.9 (3A)
unnamed: R114.1, U4.10, U5.15 (4A)

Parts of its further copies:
C15, C16, C21, C22: 100nF; C_1206_3216Metric_Pad1.33x1.80mm_HandSolder; Digikey Part Number 399-C1206C104K5RACTUCT-ND
J11, J13, J15, J17: Conn_01x04_Socket; 691412120004B; Digikey Part Number 732-691412120004B-ND
J12, J14, J16, J18: Conn_01x02_Socket; 691412120002B; Digikey Part Number 732-691412120002B-ND
R53, R54, R55, R56, R69, R70, R71, R72: 180R; R_1206_3216Metric_Pad1.30x1.75mm_HandSolder; Digikey Part Number 311-180FRCT-ND
R106, R107, R109, R110, R112, R113, R115, R116: 4K7; R_1206_3216Metric_Pad1.30x1.75mm_HandSolder; Digikey Part Number 311-4.70KFRCT-ND
U12, U14: LTV-247; SOP-16_4.4x10.4mm_P1.27mm; Digikey Part Number 160-2255-1-ND
U13, U15: AM26LS31CDR; SOIC-16_3.9x9.9mm_P1.27mm; JLCPCB Part #（optional） C3019542

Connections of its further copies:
+5VD: C15.1, C16.1, C21.1, C22.1, J11.1, J13.1, J15.1, J17.1, R106.2, R107.2, R109.2, R110.2, R112.2, R113.2, R115.2, R116.2, U13.4 (G), U13.16 (VDD), U15.4 (G), U15.16 (VDD); also elsewhere on the board
/B and C Stepper Drivers/B_DIR+: J15.4, U15.6 (2Y)
/B and C Stepper Drivers/B_DIR-: J16.1, U15.5 (2Z)
/B and C Stepper Drivers/B_STEP+: J15.2, U15.2 (1Y)
/B and C Stepper Drivers/B_STEP-: J15.3, U15.3 (1Z)
/B and C Stepper Drivers/C_DIR+: J17.4, U15.14 (4Y)
/B and C Stepper Drivers/C_DIR-: J18.1, U15.13 (4Z)
/B and C Stepper Drivers/C_STEP+: J17.2, U15.10 (3Y)
/B and C Stepper Drivers/C_STEP-: J17.3, U15.11 (3Z)
/MCU_A_DIR: R56.1; also elsewhere on the board
/MCU_A_STEP: R55.1; also elsewhere on the board
/MCU_B_DIR: R70.1; also elsewhere on the board
/MCU_B_STEP: R69.1; also elsewhere on the board
/MCU_C_DIR: R72.1; also elsewhere on the board
/MCU_C_STEP: R71.1; also elsewhere on the board
/MCU_Z_DIR: R54.1; also elsewhere on the board
/MCU_Z_STEP: R53.1; also elsewhere on the board
/Z and A Stepper Drivers/A_DIR+: J13.4, U13.14 (4Y)
/Z and A Stepper Drivers/A_DIR-: J14.1, U13.13 (4Z)
/Z and A Stepper Drivers/A_STEP+: J13.2, U13.10 (3Y)
/Z and A Stepper Drivers/A_STEP-: J13.3, U13.11 (3Z)
/Z and A Stepper Drivers/Z_DIR+: J11.4, U13.6 (2Y)
/Z and A Stepper Drivers/Z_DIR-: J12.1, U13.5 (2Z)
/Z and A Stepper Drivers/Z_STEP+: J11.2, U13.2 (1Y)
/Z and A Stepper Drivers/Z_STEP-: J11.3, U13.3 (1Z)
GNDPWR: C15.2, C16.2, C21.2, C22.2, J12.2, J14.2, J16.2, J18.2, U12.9, U12.11, U12.13, U12.15, U13.8 (GND), U13.12 (~G), U14.9, U14.11, U14.13, U14.15, U15.8 (GND), U15.12 (~G); also elsewhere on the board
GNDREF: U12.2, U12.4, U12.6, U12.8, U14.2, U14.4, U14.6, U14.8; also elsewhere on the board
unnamed: R53.2, U12.1
unnamed: R54.2, U12.3
unnamed: R55.2, U12.5
unnamed: R56.2, U12.7
unnamed: R69.2, U14.1
unnamed: R70.2, U14.3
unnamed: R71.2, U14.5
unnamed: R72.2, U14.7
unnamed: R106.1, U12.16, U13.1 (1A)
unnamed: R109.1, U12.14, U13.7 (2A)
unnamed: R112.1, U12.12, U13.9 (3A)
unnamed: R115.1, U12.10, U13.15 (4A)
unnamed: R107.1, U14.16, U15.1 (1A)
unnamed: R110.1, U14.14, U15.7 (2A)
unnamed: R113.1, U14.12, U15.9 (3A)
unnamed: R116.1, U14.10, U15.15 (4A)

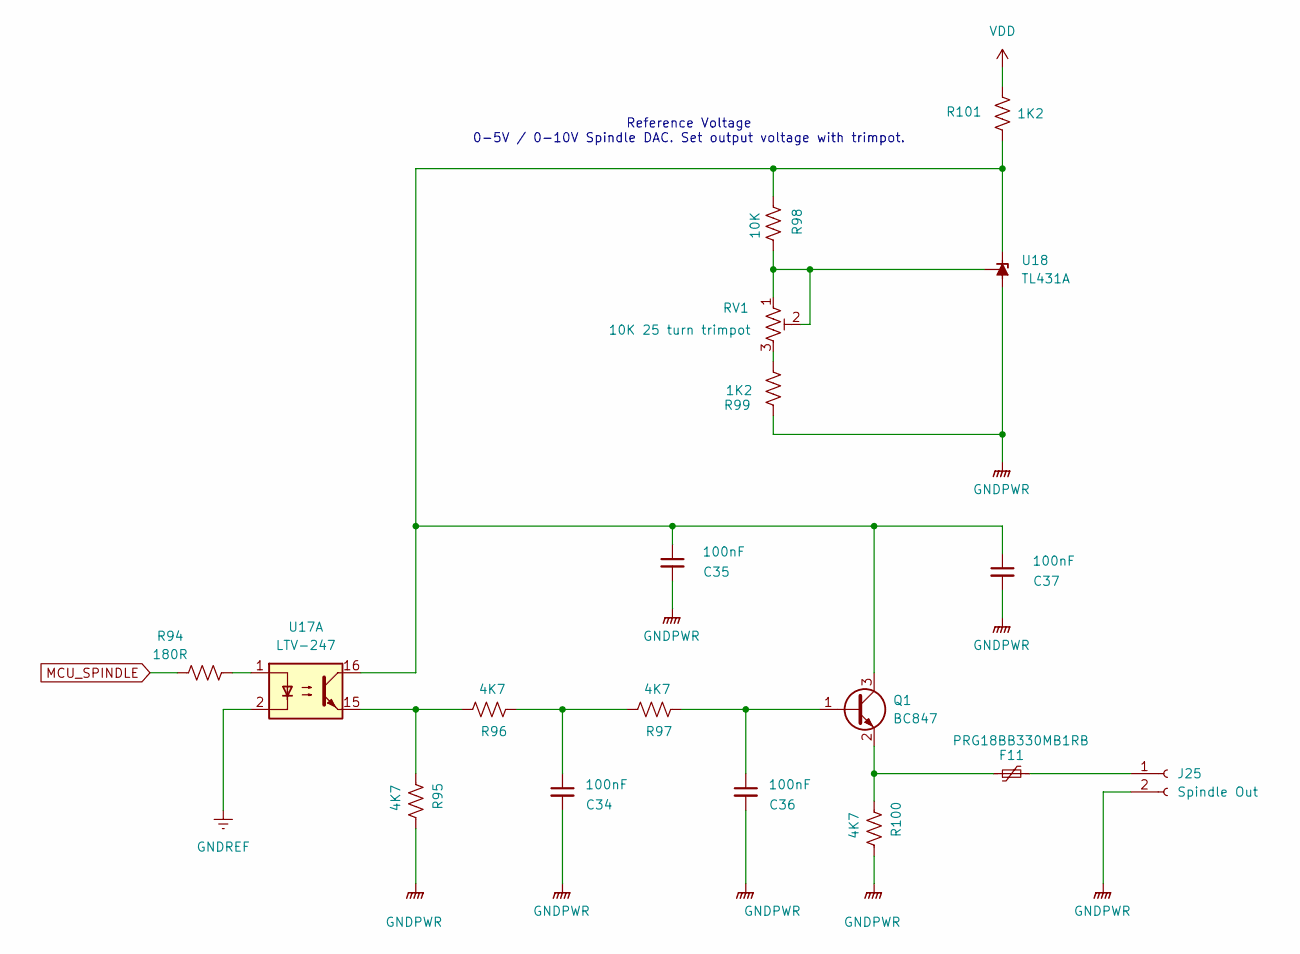
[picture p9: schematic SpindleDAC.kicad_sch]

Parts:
C34, C35, C36, C37: 100nF; C_1206_3216Metric_Pad1.33x1.80mm_HandSolder; Digikey Part Number 399-C1206C104K5RACTUCT-ND
F11: PRG18BB330MB1RB; Fuse_0603_1608Metric_Pad1.05x0.95mm_HandSolder; Digikey Part Number 490-2471-1-ND
J25: Spindle Out; 691412120002B; Digikey Part Number 732-691412120002B-ND
Q1: BC847; SOT-23; Digikey Part Number BC847CLT1GOSCT-ND
R94: 180R; R_1206_3216Metric_Pad1.30x1.75mm_HandSolder; Digikey Part Number 311-180FRCT-ND
R95, R96, R97, R100: 4K7; R_1206_3216Metric_Pad1.30x1.75mm_HandSolder; Digikey Part Number 311-4.70KFRCT-ND
R98: 10K; R_1206_3216Metric_Pad1.30x1.75mm_HandSolder; Digikey Part Number 311-10.0KFRCT-ND
R99, R101: 1K2; R_1206_3216Metric_Pad1.30x1.75mm_HandSolder; Digikey Part Number RMCF1206JT1K20CT-ND
RV1: 10K 25 turn trimpot; Potentiometer_Bourns_3266Y_Vertical; Digikey Part Number 118-PV36W103C01B00-ND
U17: LTV-247; SOP-16_4.4x10.4mm_P1.27mm; Digikey Part Number 160-2255-1-ND
U18: TL431A; SOT-23; Digikey Part Number 4878-MMTL431ACT-ND

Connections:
GNDPWR: C34.2, C35.2, C36.2, C37.2, J25.2, R95.2, R99.1, R100.2, U18.3 (A); also elsewhere on the board
GNDREF: U17.2; also elsewhere on the board
MCU_SPINDLE: R94.1; also elsewhere on the board
unnamed: C34.1, R96.1, R97.2
unnamed: F11.2, J25.1
unnamed: C36.1, Q1.1 (B), R97.1
unnamed: C35.1, C37.1, Q1.3 (C), R98.1, R101.1, U17.16, U18.2 (K)
unnamed: F11.1, Q1.2 (E), R100.1
unnamed: R94.2, U17.1
unnamed: R95.1, R96.2, U17.15
unnamed: R99.2, RV1.3
unnamed: R98.2, RV1.1, RV1.2, U18.1 (REF)
VDD: R101.2; also elsewhere on the board

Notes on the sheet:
Reference Voltage 0-5V / 0-10V Spindle DAC. Set output voltage with trimpot.

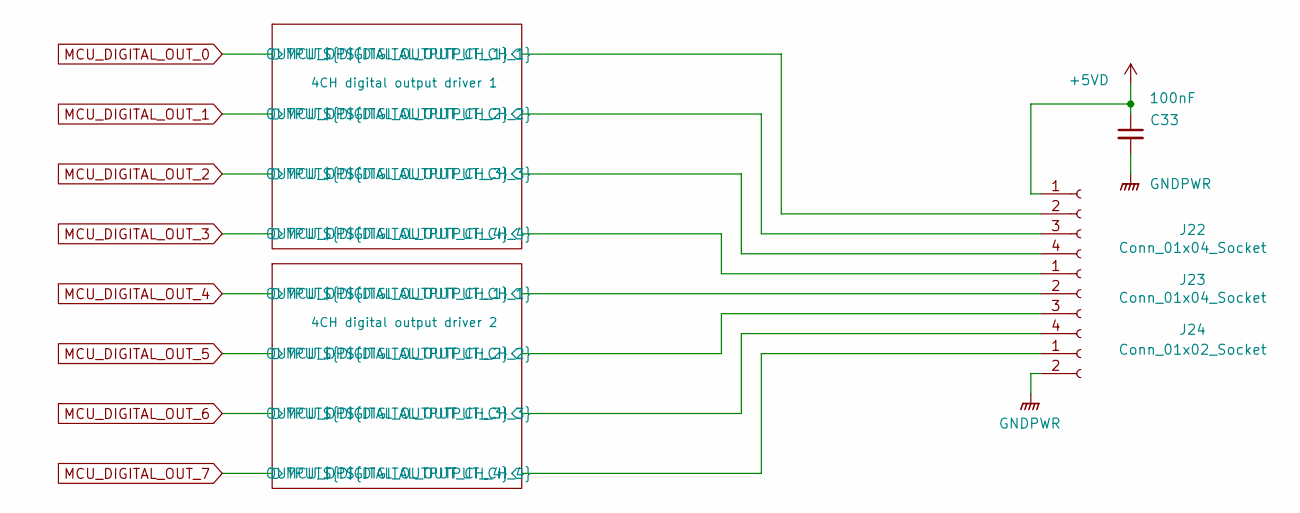
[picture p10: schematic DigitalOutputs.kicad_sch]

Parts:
C33: 100nF; C_1206_3216Metric_Pad1.33x1.80mm_HandSolder; Digikey Part Number 399-C1206C104K5RACTUCT-ND
J22, J23: Conn_01x04_Socket; 691412120004B; Digikey Part Number 732-691412120004B-ND
J24: Conn_01x02_Socket; 691412120002B; Digikey Part Number 732-691412120002B-ND

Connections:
+5VD: C33.1, J22.1; also elsewhere on the board
/Digital Outputs/4CH digital output driver 1/OUTPUT0: J22.2; also elsewhere on the board
/Digital Outputs/4CH digital output driver 1/OUTPUT1: J22.3; also elsewhere on the board
/Digital Outputs/4CH digital output driver 1/OUTPUT2: J22.4; also elsewhere on the board
/Digital Outputs/4CH digital output driver 1/OUTPUT3: J23.1; also elsewhere on the board
/Digital Outputs/4CH digital output driver 2/OUTPUT4: J23.2; also elsewhere on the board
/Digital Outputs/4CH digital output driver 2/OUTPUT5: J23.3; also elsewhere on the board
/Digital Outputs/4CH digital output driver 2/OUTPUT6: J23.4; also elsewhere on the board
/Digital Outputs/4CH digital output driver 2/OUTPUT7: J24.1; also elsewhere on the board
GNDPWR: C33.2, J24.2; also elsewhere on the board

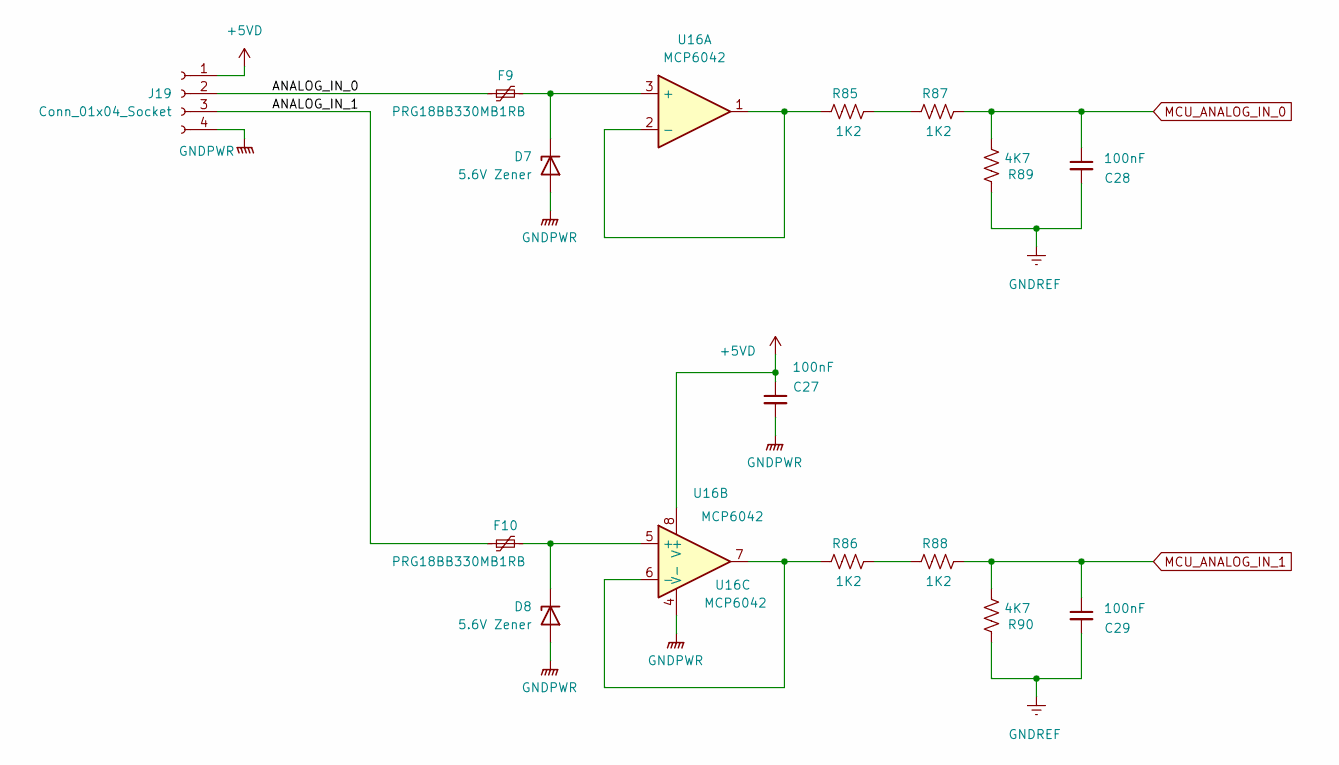
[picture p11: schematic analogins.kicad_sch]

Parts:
C27, C28, C29: 100nF; C_1206_3216Metric_Pad1.33x1.80mm_HandSolder; Digikey Part Number 399-C1206C104K5RACTUCT-ND
D7, D8: 5.6V Zener; SOT-23; Digikey Part Number SZMMBZ5232BLT1GOSCT-ND
F9, F10: PRG18BB330MB1RB; Fuse_0603_1608Metric_Pad1.05x0.95mm_HandSolder; Digikey Part Number 490-2471-1-ND
J19: Conn_01x04_Socket; 691412120004B; Digikey Part Number 732-691412120004B-ND
R85, R86, R87, R88: 1K2; R_1206_3216Metric_Pad1.30x1.75mm_HandSolder; Digikey Part Number RMCF1206JT1K20CT-ND
R89, R90: 4K7; R_1206_3216Metric_Pad1.30x1.75mm_HandSolder; Digikey Part Number 311-4.70KFRCT-ND
U16: MCP6042; SOIC-8_3.9x4.9mm_P1.27mm; Digikey Part Number MCP6042-I/SN-ND

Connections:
+5VD: C27.1, J19.1, U16.8 (V+); also elsewhere on the board
/Analog Inputs/ANALOG_IN_0: F9.1, J19.2
/Analog Inputs/ANALOG_IN_1: F10.1, J19.3
GNDPWR: C27.2, D7.1 (A), D8.1 (A), J19.4, U16.4 (V-); also elsewhere on the board
GNDREF: C28.2, C29.2, R89.1, R90.1; also elsewhere on the board
MCU_ANALOG_IN_0: C28.1, R87.1, R89.2; also elsewhere on the board
MCU_ANALOG_IN_1: C29.1, R88.1, R90.2; also elsewhere on the board
unnamed: D7.3 (K), F9.2, U16.3 (+)
unnamed: D8.3 (K), F10.2, U16.5 (+)
unnamed: R85.1, R87.2
unnamed: R86.1, R88.2
unnamed: R85.2, U16.1, U16.2 (-)
unnamed: R86.2, U16.6 (-), U16.7

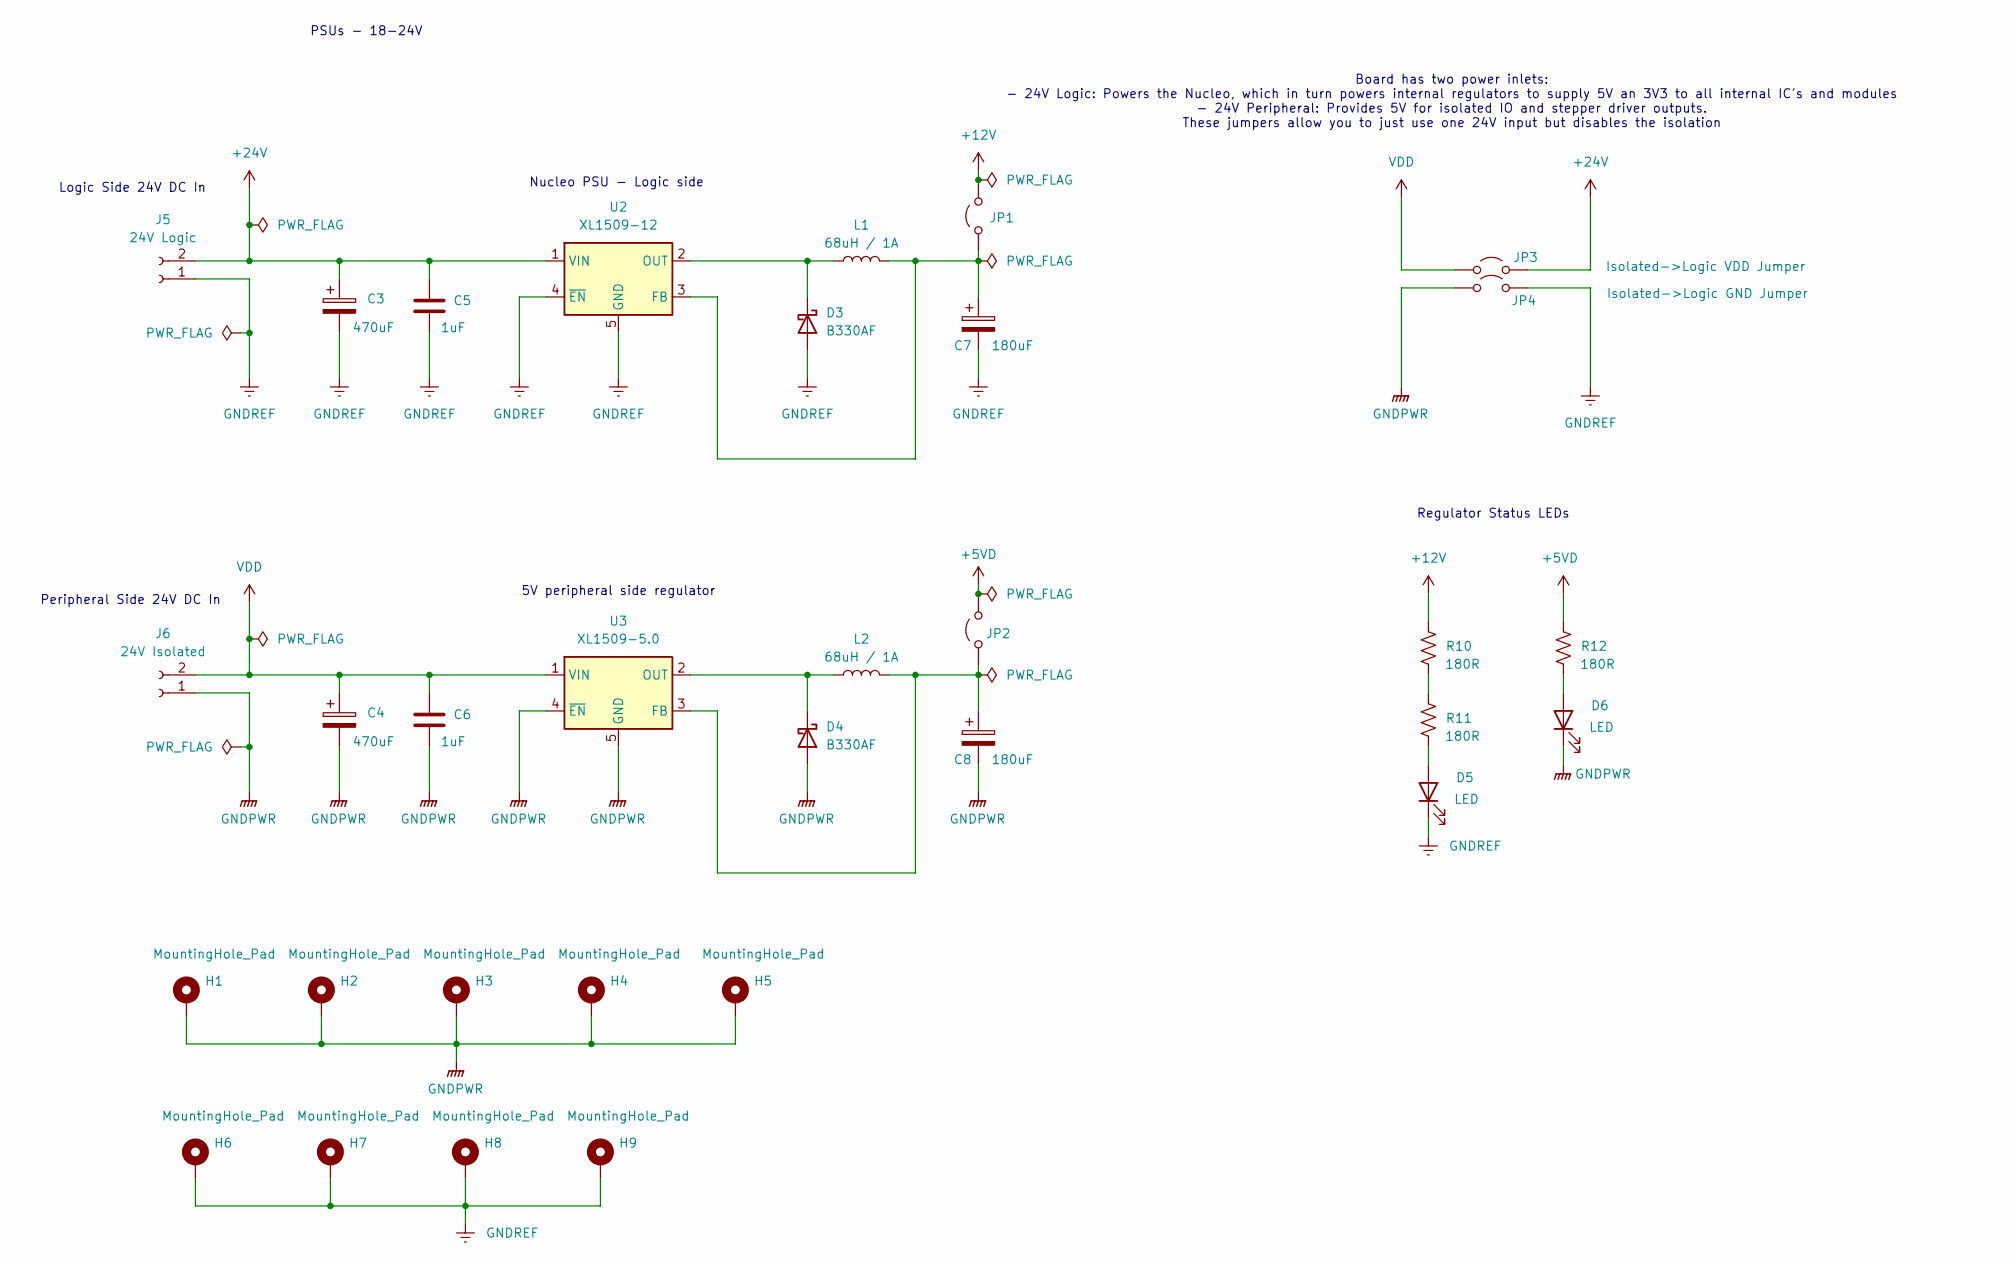
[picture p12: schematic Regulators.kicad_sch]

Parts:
C3, C4: 470uF; CP_Radial_D10.0mm_P5.00mm; Digikey Part Number 399-ESK477M050AH4KACT-ND
C5, C6: 1uF; C_1206_3216Metric_Pad1.33x1.80mm_HandSolder; Digikey Part Number 1276-1068-1-ND
C7, C8: 180uF; CP_Radial_D6.3mm_P2.50mm; Digikey Part Number 732-8633-1-ND
D3, D4: B330AF; D_SMA; Digikey Part Number B330AF-13DICT-ND
D5, D6: LED; D_1206_3216Metric_Pad1.42x1.75mm_HandSolder; Digikey Part Number 3147-B1501USD-20D000313U1930CT-ND
H1, H2, H3, H4, H5, H6, H7, H8, H9: MountingHole_Pad; MountingHole_2.7mm_M2.5_DIN965_Pad_TopBottom
J5: 24V Logic; 691412120002B; Digikey Part Number 732-691412120002B-ND
J6: 24V Isolated; 691412120002B; Digikey Part Number 732-691412120002B-ND
JP1, JP2: Peripheral->Logic VDD Jumper; SolderJumper-2_P1.3mm_Bridged2Bar_RoundedPad1.0x1.5mm; Digikey Part Number N/A
JP3: Isolated->Logic VDD Jumper; SolderJumper-2_P1.3mm_Open_RoundedPad1.0x1.5mm; Digikey Part Number N/A
JP4: Isolated->Logic GND Jumper; SolderJumper-2_P1.3mm_Open_RoundedPad1.0x1.5mm; Digikey Part Number N/A
L1, L2: 68uH / 1A; L_APV_ANR8040; Digikey Part Number SDE0805A-680KCT-ND
R10, R11, R12: 180R; R_1206_3216Metric_Pad1.30x1.75mm_HandSolder; Digikey Part Number 311-180FRCT-ND
U2: XL1509-12; SOIC-8_3.9x4.9mm_P1.27mm; Digikey Part Number 4518-XL1509-12CT-ND
U3: XL1509-5.0; SOIC-8_3.9x4.9mm_P1.27mm; Digikey Part Number 4518-XL1509-5.0CT-ND

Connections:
+5VD: JP2.2 (B), R12.1; also elsewhere on the board
+12V: JP1.2 (B), R10.1; also elsewhere on the board
+24V: C3.1, C5.1, J5.2, JP3.2 (B), U2.1 (VIN)
GNDPWR: C4.2, C6.2, C8.2, D4.2 (A), D6.1 (K), H1.1, H2.1, H3.1, H4.1, H5.1, J6.1, JP4.1 (A), U3.4 (~EN), U3.5 (GND), U3.6 (GND), U3.7 (GND), U3.8 (GND); also elsewhere on the board
GNDREF: C3.2, C5.2, C7.2, D3.2 (A), D5.1 (K), H6.1, H7.1, H8.1, H9.1, J5.1, JP4.2 (B), U2.4 (~EN), U2.5 (GND), U2.6 (GND), U2.7 (GND), U2.8 (GND); also elsewhere on the board
unnamed: D3.1 (K), L1.1, U2.2 (OUT)
unnamed: D4.1 (K), L2.1, U3.2 (OUT)
unnamed: D5.2 (A), R11.2
unnamed: D6.2 (A), R12.2
unnamed: C7.1, JP1.1 (A), L1.2, U2.3 (FB)
unnamed: C8.1, JP2.1 (A), L2.2, U3.3 (FB)
unnamed: R10.2, R11.1
VDD: C4.1, C6.1, J6.2, JP3.1 (A), U3.1 (VIN); also elsewhere on the board

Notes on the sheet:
Board has two power inlets: - 24V Logic: Powers the Nucleo, which in turn powers internal regulators to supply 5V an 3V3 to all internal IC's and modules - 24V Peripheral: Provides 5V for isolated IO and stepper driver outputs. These jumpers allow you to just use one 24V input but disables the isol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
5V peripheral side regulator
Nucleo PSU - Logic side
Logic Side 24V DC In
PSUs - 18-24V
Peripheral Side 24V DC In
Regulator Status LEDs

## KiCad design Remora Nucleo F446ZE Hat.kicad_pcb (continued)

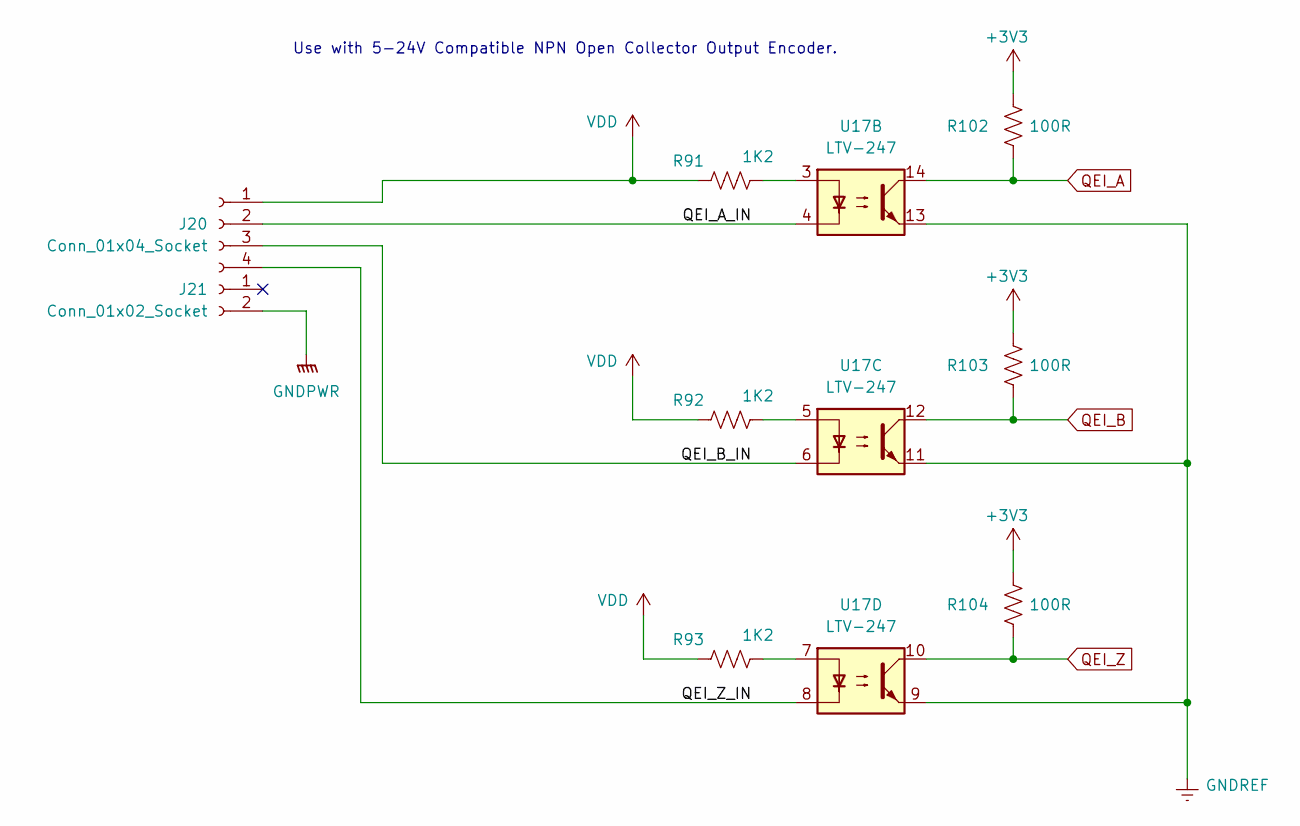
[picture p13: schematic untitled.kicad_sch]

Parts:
J20: Conn_01x04_Socket; 691412120004B; Digikey Part Number 732-691412120004B-ND
J21: Conn_01x02_Socket; 691412120002B; Digikey Part Number 732-691412120002B-ND
R91, R92, R93: 1K2; R_1206_3216Metric_Pad1.30x1.75mm_HandSolder; Digikey Part Number RMCF1206JT1K20CT-ND
R102, R103, R104: 100R; R_1206_3216Metric_Pad1.30x1.75mm_HandSolder
U17: LTV-247; SOP-16_4.4x10.4mm_P1.27mm; Digikey Part Number 160-2255-1-ND

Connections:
+3V3: R102.1, R103.1, R104.1; also elsewhere on the board
/Encoder Inputs/QEI_A_IN: J20.2, U17.4
/Encoder Inputs/QEI_B_IN: J20.3, U17.6
/Encoder Inputs/QEI_Z_IN: J20.4, U17.8
GNDPWR: J21.2; also elsewhere on the board
GNDREF: U17.9, U17.11, U17.13; also elsewhere on the board
unnamed: R91.1, U17.3
unnamed: R92.1, U17.5
unnamed: R93.1, U17.7
QEI_A: R102.2, U17.14; also elsewhere on the board
QEI_B: R103.2, U17.12; also elsewhere on the board
QEI_Z: R104.2, U17.10; also elsewhere on the board
VDD: J20.1, R91.2, R92.2, R93.2; also elsewhere on the board

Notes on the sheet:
Use with 5-24V Compatible NPN Open Collector Output Encoder.

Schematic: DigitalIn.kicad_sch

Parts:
R33, R34, R35, R36: 180R; R_1206_3216Metric_Pad1.30x1.75mm_HandSolder; Digikey Part Number 311-180FRCT-ND
U7: LTV-247; SOP-16_4.4x10.4mm_P1.27mm; Digikey Part Number 160-2255-1-ND

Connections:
+5VD: R33.1, R34.1, R35.1, R36.1; also elsewhere on the board
/Digital Inputs/Digital Input 4-7/INPUT4: U7.2; also elsewhere on the board
/Digital Inputs/Digital Input 4-7/INPUT5: U7.4; also elsewhere on the board
/Digital Inputs/Digital Input 4-7/INPUT6: U7.6; also elsewhere on the board
/Digital Inputs/Digital Input 4-7/INPUT7: U7.8; also elsewhere on the board
GNDREF: U7.9, U7.11, U7.13, U7.15; also elsewhere on the board
MCU_DIGITAL_IN_4: U7.16; also elsewhere on the board
MCU_DIGITAL_IN_5: U7.14; also elsewhere on the board
MCU_DIGITAL_IN_6: U7.12; also elsewhere on the board
MCU_DIGITAL_IN_7: U7.10; also elsewhere on the board
unnamed: R33.2, U7.1
unnamed: R34.2, U7.3
unnamed: R35.2, U7.5
unnamed: R36.2, U7.7

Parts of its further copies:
R41, R42, R43, R44, R45, R46, R47, R48, R49, R50, R51, R52: 180R; R_1206_3216Metric_Pad1.30x1.75mm_HandSolder; Digikey Part Number 311-180FRCT-ND
U9, U10, U11: LTV-247; SOP-16_4.4x10.4mm_P1.27mm; Digikey Part Number 160-2255-1-ND

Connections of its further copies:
+5VD: R41.1, R42.1, R43.1, R44.1, R45.1, R46.1, R47.1, R48.1, R49.1, R50.1, R51.1, R52.1; also elsewhere on the board
/Digital Inputs/Digital Input 0-3/INPUT0: U11.2; also elsewhere on the board
/Digital Inputs/Digital Input 0-3/INPUT1: U11.4; also elsewhere on the board
/Digital Inputs/Digital Input 0-3/INPUT2: U11.6; also elsewhere on the board
/Digital Inputs/Digital Input 0-3/INPUT3: U11.8; also elsewhere on the board
/Digital Inputs/Digital Input 8-11/INPUT8: U9.2; also elsewhere on the board
/Digital Inputs/Digital Input 8-11/INPUT9: U9.4; also elsewhere on the board
/Digital Inputs/Digital Input 8-11/INPUT10: U9.6; also elsewhere on the board
/Digital Inputs/Digital Input 8-11/INPUT11: U9.8; also elsewhere on the board
/Digital Inputs/Digital Input 12-15/INPUT12: U10.2; also elsewhere on the board
/Digital Inputs/Digital Input 12-15/INPUT13: U10.4; also elsewhere on the board
/Digital Inputs/Digital Input 12-15/INPUT14: U10.6; also elsewhere on the board
/Digital Inputs/Digital Input 12-15/INPUT15: U10.8; also elsewhere on the board
GNDREF: U9.9, U9.11, U9.13, U9.15, U10.9, U10.11, U10.13, U10.15, U11.9, U11.11, U11.13, U11.15; also elsewhere on the board
MCU_DIGITAL_IN_0: U11.16; also elsewhere on the board
MCU_DIGITAL_IN_1: U11.14; also elsewhere on the board
MCU_DIGITAL_IN_2: U11.12; also elsewhere on the board
MCU_DIGITAL_IN_3: U11.10; also elsewhere on the board
MCU_DIGITAL_IN_8: U9.16; also elsewhere on the board
MCU_DIGITAL_IN_9: U9.14; also elsewhere on the board
MCU_DIGITAL_IN_10: U9.12; also elsewhere on the board
MCU_DIGITAL_IN_11: U9.10; also elsewhere on the board
MCU_DIGITAL_IN_12: U10.16; also elsewhere on the board
MCU_DIGITAL_IN_13: U10.14; also elsewhere on the board
MCU_DIGITAL_IN_14: U10.12; also elsewhere on the board
MCU_DIGITAL_IN_15: U10.10; also elsewhere on the board
unnamed: R41.2, U9.1
unnamed: R42.2, U9.3
unnamed: R43.2, U9.5
unnamed: R44.2, U9.7
unnamed: R45.2, U10.1
unnamed: R46.2, U10.3
unnamed: R47.2, U10.5
unnamed: R48.2, U10.7
unnamed: R49.2, U11.1
unnamed: R50.2, U11.3
unnamed: R51.2, U11.5
unnamed: R52.2, U11.7

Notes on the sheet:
NPN Inputs

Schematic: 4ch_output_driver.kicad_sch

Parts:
F1, F2, F3, F4: PRG18BB330MB1RB; Fuse_0603_1608Metric_Pad1.05x0.95mm_HandSolder; Digikey Part Number 490-2471-1-ND
R29, R30, R31, R32: 180R; R_1206_3216Metric_Pad1.30x1.75mm_HandSolder; Digikey Part Number 311-180FRCT-ND
U6: LTV-247; SOP-16_4.4x10.4mm_P1.27mm; Digikey Part Number 160-2255-1-ND

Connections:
/Digital Outputs/4CH digital output driver 1/OUTPUT0: F1.2; also elsewhere on the board
/Digital Outputs/4CH digital output driver 1/OUTPUT1: F2.2; also elsewhere on the board
/Digital Outputs/4CH digital output driver 1/OUTPUT2: F3.2; also elsewhere on the board
/Digital Outputs/4CH digital output driver 1/OUTPUT3: F4.2; also elsewhere on the board
GNDPWR: U6.9, U6.11, U6.13, U6.15; also elsewhere on the board
GNDREF: U6.2, U6.4, U6.6, U6.8; also elsewhere on the board
MCU_DIGITAL_OUT_0: R29.1; also elsewhere on the board
MCU_DIGITAL_OUT_1: R30.1; also elsewhere on the board
MCU_DIGITAL_OUT_2: R31.1; also elsewhere on the board
MCU_DIGITAL_OUT_3: R32.1; also elsewhere on the board
unnamed: F1.1, U6.16
unnamed: F2.1, U6.14
unnamed: F3.1, U6.12
unnamed: F4.1, U6.10
unnamed: R29.2, U6.1
unnamed: R30.2, U6.3
unnamed: R31.2, U6.5
unnamed: R32.2, U6.7

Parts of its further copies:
F5, F6, F7, F8: PRG18BB330MB1RB; Fuse_0603_1608Metric_Pad1.05x0.95mm_HandSolder; Digikey Part Number 490-2471-1-ND
R37, R38, R39, R40: 180R; R_1206_3216Metric_Pad1.30x1.75mm_HandSolder; Digikey Part Number 311-180FRCT-ND
U8: LTV-247; SOP-16_4.4x10.4mm_P1.27mm; Digikey Part Number 160-2255-1-ND

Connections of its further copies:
/Digital Outputs/4CH digital output driver 2/OUTPUT4: F5.2; also elsewhere on the board
/Digital Outputs/4CH digital output driver 2/OUTPUT5: F6.2; also elsewhere on the board
/Digital Outputs/4CH digital output driver 2/OUTPUT6: F7.2; also elsewhere on the board
/Digital Outputs/4CH digital output driver 2/OUTPUT7: F8.2; also elsewhere on the board
GNDPWR: U8.9, U8.11, U8.13, U8.15; also elsewhere on the board
GNDREF: U8.2, U8.4, U8.6, U8.8; also elsewhere on the board
MCU_DIGITAL_OUT_4: R37.1; also elsewhere on the board
MCU_DIGITAL_OUT_5: R38.1; also elsewhere on the board
MCU_DIGITAL_OUT_6: R39.1; also elsewhere on the board
MCU_DIGITAL_OUT_7: R40.1; also elsewhere on the board
unnamed: F5.1, U8.16
unnamed: F6.1, U8.14
unnamed: F7.1, U8.12
unnamed: F8.1, U8.10
unnamed: R37.2, U8.1
unnamed: R38.2, U8.3
unnamed: R39.2, U8.5
unnamed: R40.2, U8.7

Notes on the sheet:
NPN Outputs

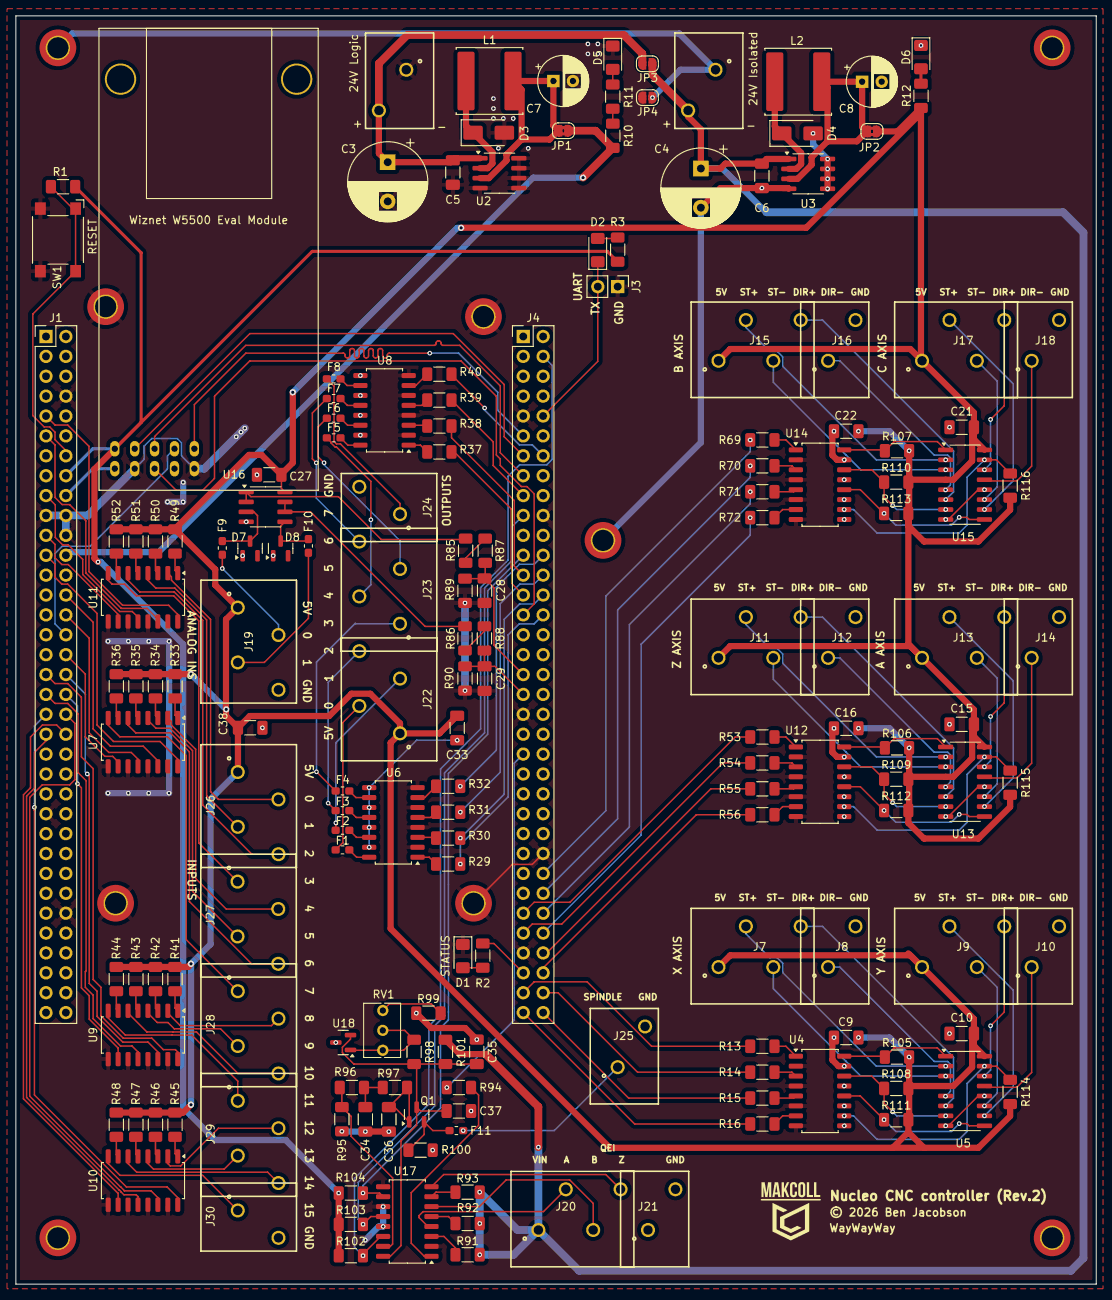
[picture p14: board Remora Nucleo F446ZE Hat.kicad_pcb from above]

Board: 2 copper layers, 138.0 x 162.0 mm, 179 parts (0 on the bottom side), 194 nets.

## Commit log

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2025-06-04 remapping IO pins around unavailable IO on board. Steppers are still in progress
    [GPIO Mapping.xlsx]
2025-06-04 Moved UART to use STLink default comms port, frees up 2x GPIO
    [GPIO Mapping.xlsx]
2025-06-04 Bug no longer reproducible with ZDir. excel mapping is now reflective of what works in software
    [GPIO Mapping.xlsx]
2025-06-04 updates to some testing, all GPIO and stepper pins now work. Yet to test ABC axis as I don't have any example GCode for it. will have to trust that 5 axis works for now
    [GPIO Mapping.xlsx]
2025-06-15 Changed board spec from Nucleo F446RE to F446ZE Altered readme to suit it and moved the Todos over.
    [Regulators.kicad_sch, Remora Nucleo F446RE Hat.kicad_pcb, Remora Nucleo F446ZE Hat.kicad_pcb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]
2025-06-15 tweaked board edge cuts, mouting hole positions and pin headers to match mechanical drawing. Yet to validate with physical hardware
    [Remora Nucleo F446ZE Hat.kicad_pcb, Remora Nucleo F446ZE Hat.kicad_sch]
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2025-06-16 changes some unecessary global labels to local. Added a heirarchical sheet for output driver and basic numbering. Sink logic not yet set for O/Ps, but placeholder for now
    [2ch_output_driver.kicad_sch, Regulators.kicad_sch, Remora Nucleo F446ZE Hat.kicad_pcb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]
2025-06-16 added reset button, programmable user button, user LED and updates to todos
    [Remora Nucleo F446ZE Hat.kicad_sch]
2025-06-17 fixed error in placement of usr_button and pull down config
    [Remora Nucleo F446ZE Hat.kicad_sch]
2025-06-17 redrew stepper drivers as duplicatable heirarchical sheets, moved jumpers into power managemente sheet, moved LEDs and user buttons into own sheet to save space. Fixed a few random labelling issues.
    [Regulators.kicad_sch, Remora Nucleo F446ZE Hat.kicad_sch, Stepper_drivers.kicad_sch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]
2025-06-17 Found a bug in the circuit, using the wrong isolated tranceivers, fixed.
    [2ch_output_driver.kicad_sch, Stepper_drivers.kicad_sch, buttons_LEDs.kicad_sch]
2025-06-18 Completed design for digital outputs, tidied into own sheets and bussing for scalability
    [1ch_output_driver.kicad_sch, DigitalOutputs.kicad_sch, Regulators.kicad_sch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]
2025-06-20 tidy of some sheets. Added 0-10V DAC, but untested - only some basic validation on simulator for now
    [1ch_output_driver.kicad_sch, DigitalOutputs.kicad_sch, Regulators.kicad_sch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]
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2025-06-21 buffered output on spindle DAC, tweak to gain structure and update to readme
    [SpindleDAC.kicad_sch]
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2025-06-26 Deleted stale test production files. Fixed up a bug with power isolation. Created some footprints for wire to board connectors although ran out of time to fix a bug where they do no lock in. Fixes to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
    [1ch_output_driver.kicad_sch, Digikey BOM.xls, DigitalIn.kicad_sch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]
2025-07-01 restructured power supplies to enable Spindle DAC to be isolated. We now have the option of supplying two 24V inputs, one to power the nucleo and everything logic side and the other to power peripher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
    [1ch_output_driver.kicad_sch, DigitalIn.kicad_sch, DigitalOutputs.kicad_sch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]
2025-07-04 Fixes to screw terminal footprints, updated BOM and included in project folder
    [Digikey BOM.xls, DigitalOutputs.kicad_sch, EBWA-02-A.step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]
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2025-09-29 moved SPI1_CS to new place. Added MicroSD card and SDIO interface to schematic
    [Remora Nucleo F446ZE Hat.kicad_sch]
2025-09-30 Fixes to bypass caps in micro SD + imported and assigned footprint file
    [Digikey BOM.xls, Remora Nucleo F446ZE Hat.kicad_pcb, Remora Nucleo F446ZE Hat.kicad_sch]
2025-10-01 Fixed bug with lack of pin header for CN11 and CN12. Addeded RPI header and aligned it, assigned some safe footprints
    [1ch_output_driver.kicad_sch, DigitalOutputs.kicad_sch, Remora Nucleo F446ZE Hat.kicad_pcb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]
2025-10-02 corrected hole spacing for Nucleo board. Double checked some of the standoff spacing and made some correction to pin header insulation heights and standoff heights too.
    [Digikey BOM.xls, Remora Nucleo F446ZE Hat.kicad_pcb]
2025-10-05 updates to read me, marked V1 parts inactive and made start on board layout for initial test board. fixes to BOM to suit
    [1ch_output_driver.kicad_sch, Digikey BOM.xls, DigitalIn.kicad_sch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]
2025-10-07 Dropped number of IO on design to make more room. Created the new footprints to suit them, updates to BOM and ran some traces on the PCB.
    [1ch_output_driver.kicad_sch, Digikey BOM.xls, DigitalIn.kicad_sch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]
2025-10-11 New optocoupler part choice, removed digikey BOM as have started inputting them into symbol fields. Re-enabled all disabled parts for now and will re-design power supplies soon.
    [4ch_output_driver.kicad_sch, Digikey BOM.xls, DigitalIn.kicad_sch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]
2025-10-11 fix to annoying additional symbol fields displaying when we didn't want them to.
    [4ch_output_driver.kicad_sch, DigitalIn.kicad_sch, DigitalOutputs.kicad_sch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]
2025-10-15 BOM consolidation for various resistors. Moved BOM into symbol libraries and updated supplimentary BOM. Switched IO optical isolation circuitry to a more cost effective part.
    [4ch_output_driver.kicad_sch, DigitalIn.kicad_sch, DigitalOutputs.kicad_sch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]
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2025-10-15 Corrections to digital input pins
    [Remora Nucleo F446ZE Hat.kicad_sch]
2025-10-17 more BOM consolidation. Switched out IO for vertical toolless wire to board terminals and added footprints. Put new isolated ground plane on board.
    [DigitalOutputs.kicad_sch, Inputs.kicad_sch, Regulators.kicad_sch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]
2025-10-18 Swapped out stepper isolators to use same as others. further BOM consolidation. Fixed bug with incorrect differential driver footprint.
    [Remora Nucleo F446ZE Hat.kicad_pcb, Remora Nucleo F446ZE Hat.kicad_sch, Stepper_drivers.kicad_sch]
2025-10-22 Built up stepper driver circuit on breadboard and tested up to 100khz, made some tweaks and happy to report this part of the design is now validated
    [Remora Nucleo F446ZE Hat.kicad_sch, Stepper_drivers.kicad_sch]
2025-11-01 Tweaks to stepper driver circuitry after some validation on breadboard. IO now fully validated
    [Stepper_drivers.kicad_sch]
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2025-11-21 New PSU designs + footprints assigned. Changes to board shape to make room for new components. BOM consolidation of supplimentary file
    [4ch_output_driver.kicad_sch, DigitalIn.kicad_sch, DigitalOutputs.kicad_sch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]
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2025-12-03 Added Analog inputs, updates to readme re powering board from external supply
    [DigitalIn.kicad_sch, DigitalOutputs.kicad_sch, Inputs.kicad_sch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]
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2026-02-06 Added high speed encoder input circuitry. General tidy and updates to readme
    [4ch_output_driver.kicad_sch, DigitalIn.kicad_sch, DigitalOutputs.kicad_sch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]
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2026-03-22 Switched terminal footprints over to a finer pitch. Corrected an issue with component reference values preventing proper use of multi channel rule areas. Component references for 4 channel optos are 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
    [691412120004B+(rev1).stp, DigitalIn.kicad_sch, DigitalOutputs.kicad_sch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]
2026-03-22 Added 3d Models for new terminal connectors for easy board verification before committing to build
    [DigitalOutputs.kicad_sch, Inputs.kicad_sch, SpindleDAC.kicad_sch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]
2026-03-29 Redo of layout to use smaller terminals, applied to steppers and inputs and laid out outputs too
    [Remora Nucleo F446ZE Hat.kicad_pcb]
2026-03-29 Quick QEI addin. Fixed clearance issues for mounting screw
    [Remora Nucleo F446ZE Hat.kicad_pcb]
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2026-03-31 Spindle out layout, rejigged QEI and moved it, minor tweak to PSU positioning
    [Remora Nucleo F446ZE Hat.kicad_pcb]
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2026-04-04 Caught some errors with spacing of jumpers, did some BOM consolidation and included BOM. Updates to Gerbers to reflect new changes.
    [DigitalIn.kicad_sch, Regulators.kicad_sch, Remora Nucleo F446ZE Hat BOM.csv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]
2026-04-04 Should not include zip files in this repo, almost committed an incorrect file. Delete now
    [Supplementary BOM.xls]
2026-04-05 About to order PCB, checked pinouts on ordered parts, reannotated and one last DRC before exporting final gerbers
    [Remora Nucleo F446ZE Hat-B_Cu.gbr, Remora Nucleo F446ZE Hat-B_Mask.gbr, Remora Nucleo F446ZE Hat-B_Paste.gbr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]
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2026-04-28 Fixed error in opamp part number
    [Remora Nucleo F446ZE Hat BOM.csv, analogins.kicad_sch]
2026-05-20 Fixed found issue with oversized regulator input cap
    [Regulators.kicad_sch, Remora Nucleo F446ZE Hat.kicad_pcb]
2026-06-02 Updates to readme, working through testing and validation of board. Corrected pull ups on differential stepper outputs. Slight tweak to encoder. Tidied up some traces. Somehow lost the mounting holes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
    [Remora Nucleo F446ZE Hat.kicad_pcb, Stepper_drivers.kicad_sch, untitled.kicad_sch]
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2026-06-03 fixed incorrect labels
    [Remora Nucleo F446ZE Hat.kicad_pcb]

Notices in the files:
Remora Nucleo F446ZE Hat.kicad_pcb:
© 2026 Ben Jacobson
